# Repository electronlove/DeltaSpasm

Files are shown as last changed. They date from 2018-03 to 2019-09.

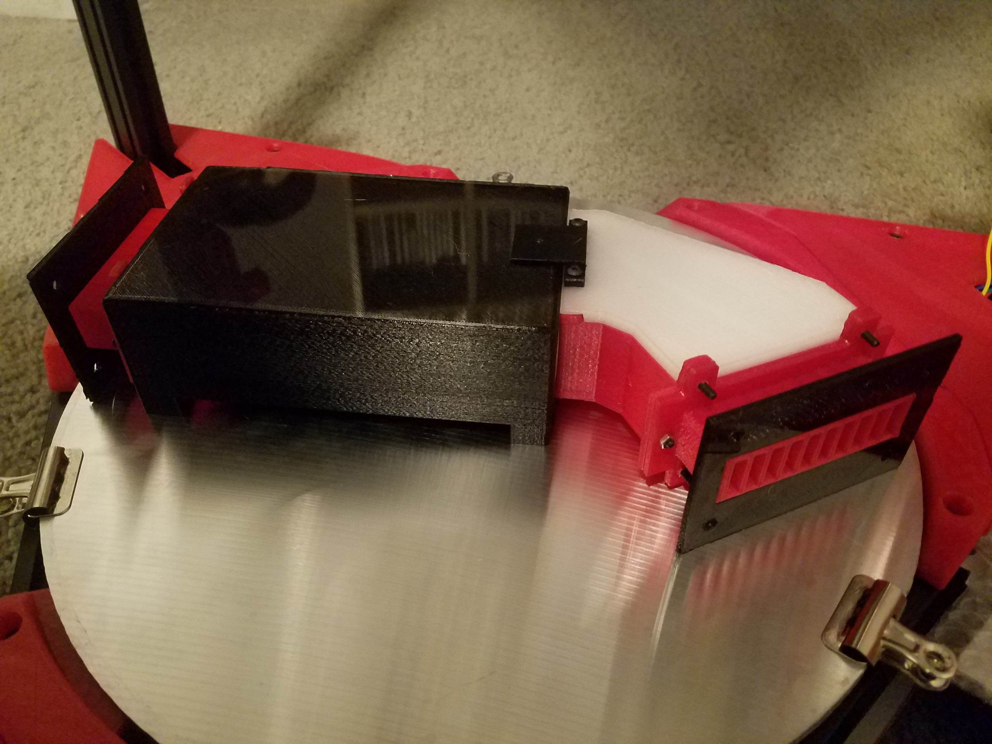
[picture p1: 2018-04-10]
Images/Cooling Fan Assembly Printed.jpg

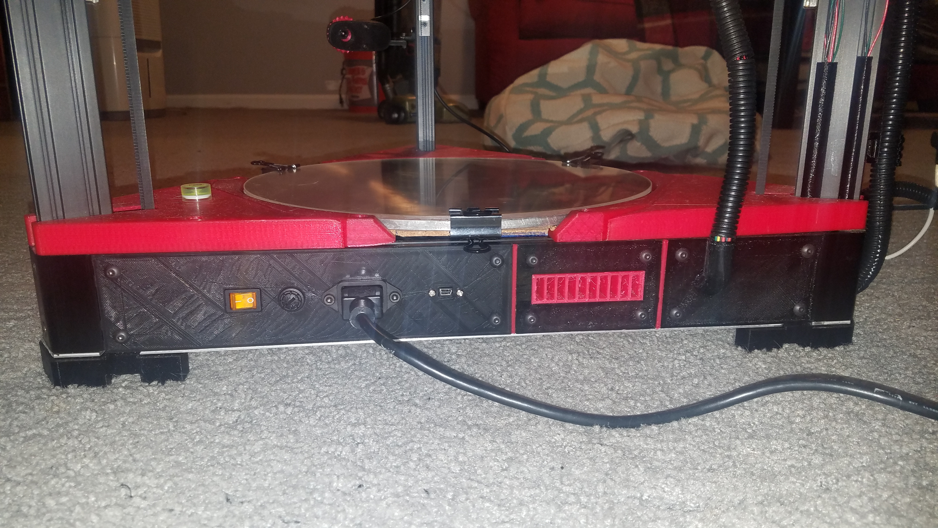
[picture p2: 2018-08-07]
Images/Delta Printer Back Panel.jpg

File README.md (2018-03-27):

# DeltaSpasm

**Larger format, 1M high Delta 3D Printer**
- **Mechanical**
  - Features a large, 310 mm build area with a 330 mm (13") x 6.25mm (0.25") MIC-6 aluminum bed.  I sourced the MIC-6 locally, from BMG Metals (Maryland).  The aluminum plate was plasma cut and the rough edges needed to be cleaned up with a Dremel !  
  - Printing surface will be 330 mm (13") x 3.175 mm (1/8") borofloat glass.  Glass will be sourced from http://www.behrenbergglass.com or www.howardglass.com at ~ $30 per plate.
  - Misumi Black Oxide 2020 and 2040 extrusions at 455mm (horizontals) and 1000mm (vertical).  
  - Delta 2040 corners from RobotDigg.  I purchased mine from an unknown Alibaba Company for a reasonable price (http://jing-bang.en.alibaba.com) 
  - 750 mm MGN12 linear rails from Jugetek (https://www.jugetek.com/) 

- **Electronics**
  - 3x 0.9° stepper motors, Model # 17HM19-1684S from Stepper Online (https://www.omc-stepperonline.com)
  - 3x Hall Endstops from Sainsmart (https://www.sainsmart.com/products/hall-effect-sensor-switch-magnetic-detector-module-for-arduino-motor)
  - 120V, 350W Silicone Heater controlled by a Crydom panel-mount SSR - Model D2425 (http://www.crydom.com/en/products/panel-mount/perfect-fit/ac-output/series-1/)
  - Meanwell 24V 350W power supply, model # LRS-350-24
  - Replicape + Beaglebone Black (https://www.thing-printer.com/)

See additional files  for BOM (xls) and STLs

Edited March 2018

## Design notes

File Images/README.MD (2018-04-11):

- The bed holders (Bed Holder.jpg) are designed to support a 13" (330 mm) x 0.25" (6.25 mm) aluminum tooling plate that is heated by a 310 mm silicone heater.  There is 13 mm clearance to accomodate (a) 6.35 mm aluminum plate (b) 4 mm cork sheet (c) 3.175 mm glass plate.  One of the bed holders is notched to allow for clearance of the bed heater wires and thermistor.  
- A set of motor covers (See *.jpg files - Motor Covers Bottom and Top for differences) prevent debris from falling into the stepper motors and finish off the top of the printing surface.  There are two types, one of which has increased clearance on the sides to accomodate wires running along the sides of the 2040 extrusions

- Hall Endstops (Hall endstop.jpg) are mounted to holders and include modified carriages that accomodate small N50 super magnets

- The Cooling Fan Assembly (Cooling fan Assembly Printed.jpg) is designed for use with Beaglebone Black and Replicapae to keep the electronics isolated from the bottom of the bed heater and motor compartments and provide for directed cooling.  It may be necessary to include an additional fan for a push/pull configuration.

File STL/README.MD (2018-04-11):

**Information on STL files**

**Endstop Holders**
- https://www.thingiverse.com/thing:2842147
- Two parts - Hall endstop holder and modified carriage with mounting point for neodymium magnets
- **File names:** Delta Hall Holder.stl and Delta_carriage_DSM.stl (Print 3X of each)

**Print Bed Surface**
  - The print bed holders are two types, one has a notch for the AC mains + thermistor wire of a silicone heater to go underneath the print bed and the other two do not.
  - 4mm thick cork should be glued in place to protect the mounts from heat damage (Mine were printed in PETG but ABS or ASA is preferable)
  - Holders use 5mm socket cap screws and t-nuts.
  - Designed to accommodate a 330 mm (13") bed and 455mm horizontal extrusions.
  - **File names:** Delta Bed Holder V1.stl (Print 2X) and Delta Bed Holder wire guide 15mm.stl (Print 1X)
  
**Motor Covers**
  - The motor covers are of two types, one has a larger notch to accomodate wiring and guide it beneath the print bed.  
  - Motor covers use 5mm socket cap screws and t-nuts.
  - Designed to accommodate a 330 mm (13") bed and 455mm horizontal extrusions.  
  - **File names:** Delta motor covers normal clean.stl (Print 2X) and Delta motor covers wire  clean.stl (Print 1X)
  
**Electronics Cooling**
  - https://www.thingiverse.com/thing:2855541
  - Consists of 2x fan grills that are 20mm in height, a fan mount for 2x 30mm fans, and a cover for BBB + replicape
  - The BBB + cape are screwed into the bottom aluminmum bottom plate / heatsink) with brass stand-offs.
  - **File names:** Fan conduit Cover V2.stl, Fan Conduit.stl, Fan Grill.stl, Cape enclosure.stl 
 
 **Other Mechanical Parts**
  - 3X Feet to raise the bottom of the Delta Printer for optional airflow in the bottom compartment and vibration isolation
  - **File names:** Delta Feet.stl
  - Panel for IEC connector, Bulgin fuse holder(Part # FX0462), and Illuminated Mains Switch (Part # H8553VBBA3-551W)
  - **File name:** Delta Power Panel.stl 
  - Panel for Panel Mount Ethernet and USB cables to Beaglebone Black (Adafruit Part # 909 and 908)
  - **File name:** ENET USB Panel.stl
  - Bottom design/heatsink for electronics and mounting holes - For CNC/laser/plasma what-have-you
  - **File name:** Delta_09_mount_t.dxf

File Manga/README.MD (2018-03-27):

**Display enclosure for 5.8" Manga Screen**

See also https://www.thingiverse.com/thing:2810512

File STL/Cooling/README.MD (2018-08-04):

Info for the Cooling Unit and Electronics Mounts

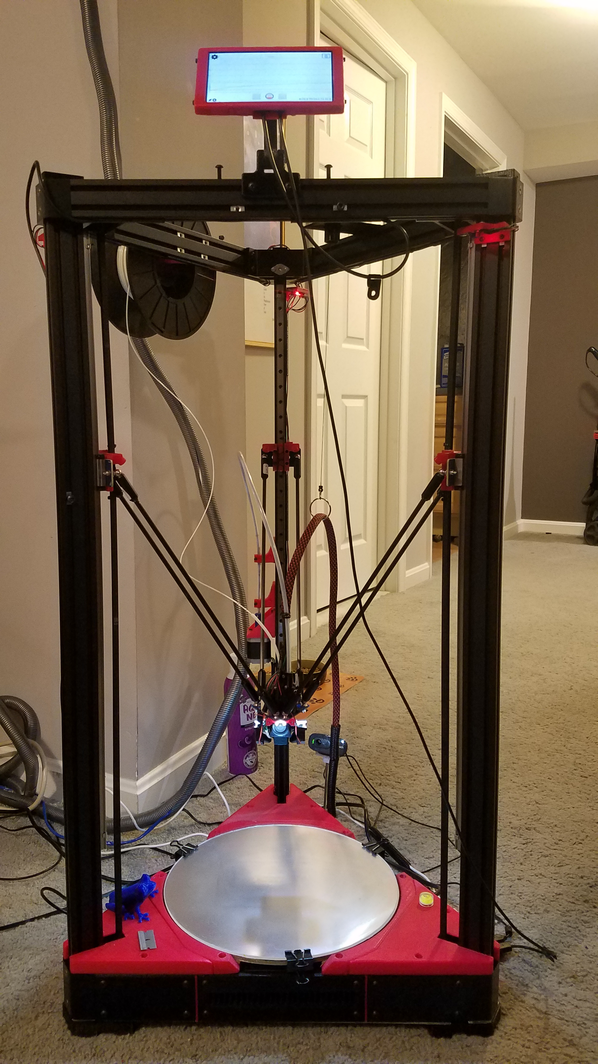
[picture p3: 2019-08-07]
DeltaSpasm_082019.jpg

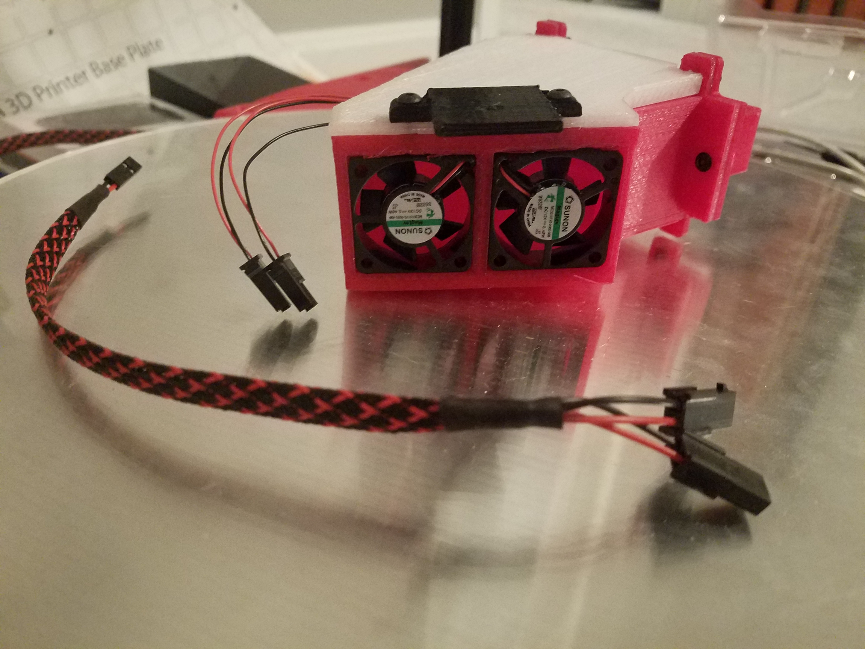
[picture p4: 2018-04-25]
Images/Cooling Fans.jpg

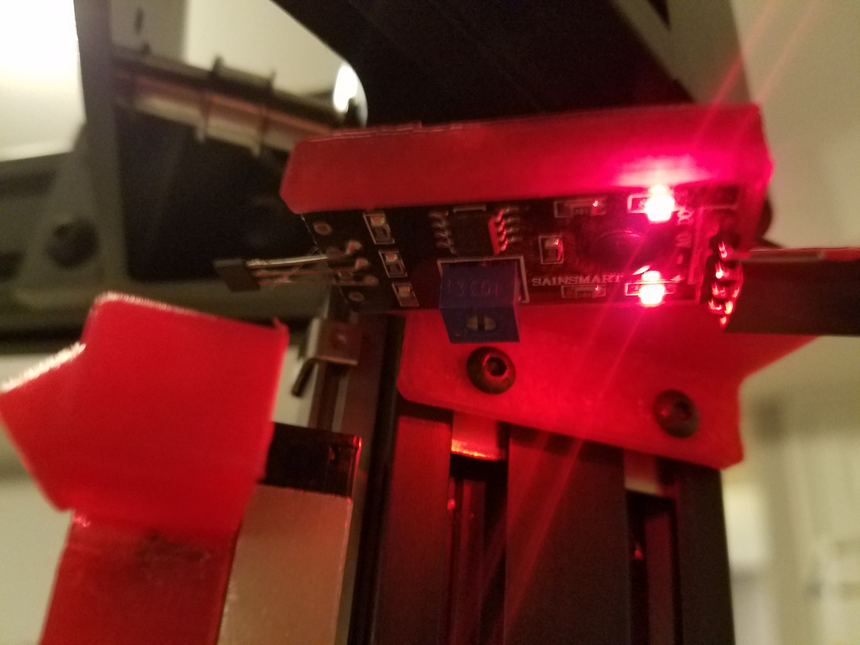
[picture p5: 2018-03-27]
Images/Hall Endstops Active.jpg

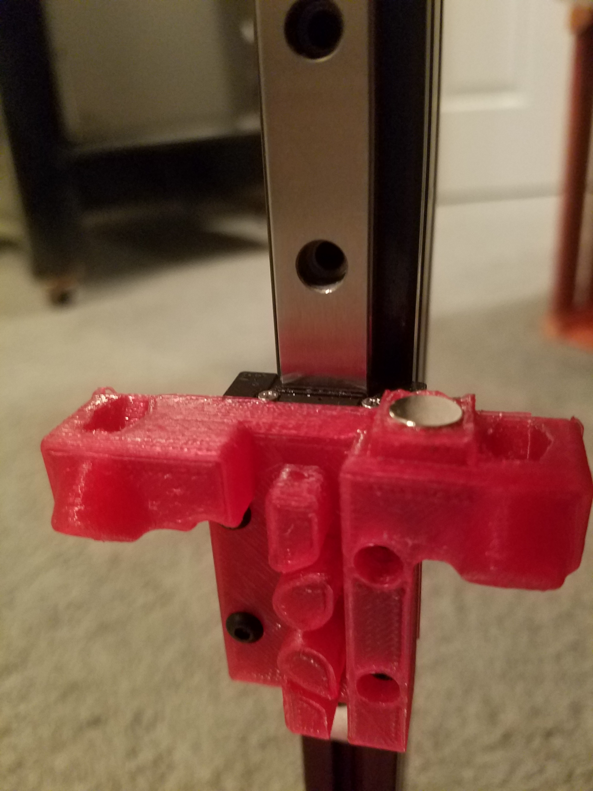
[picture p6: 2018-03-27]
Images/Carriage with N50 magnets.jpg

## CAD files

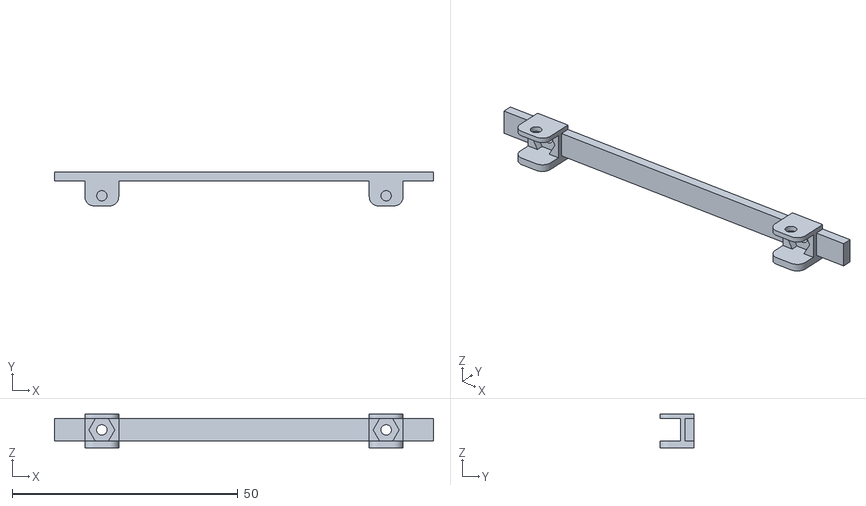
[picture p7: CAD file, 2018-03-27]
Manga/Case Brace Assembly.stl
84.0 x 7.50 x 7.50

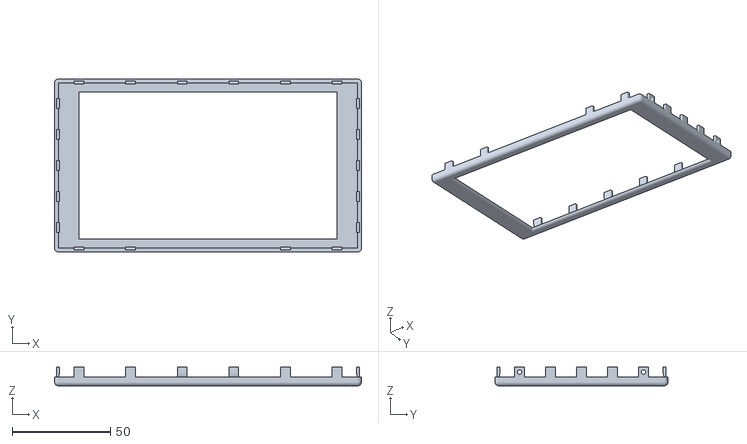
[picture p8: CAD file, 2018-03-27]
Manga/Bezel V2.stl
156.0 x 88.0 x 9.50

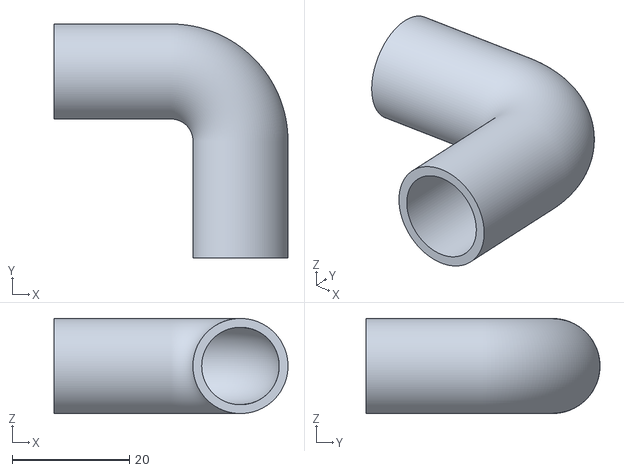
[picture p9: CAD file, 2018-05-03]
STL/Effector Wire Conduit.stl
40.0 x 40.0 x 16.2

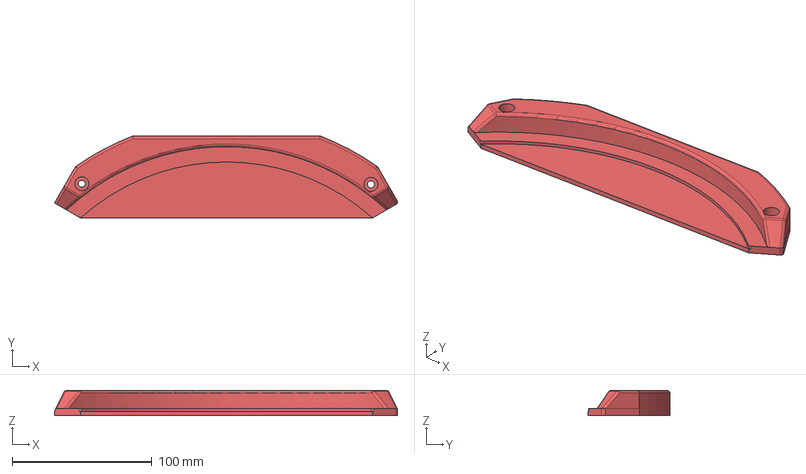
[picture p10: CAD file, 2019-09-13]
CAD/Delta Bed Holder without guide.stp
245.3 x 58.6 x 18.0 mm

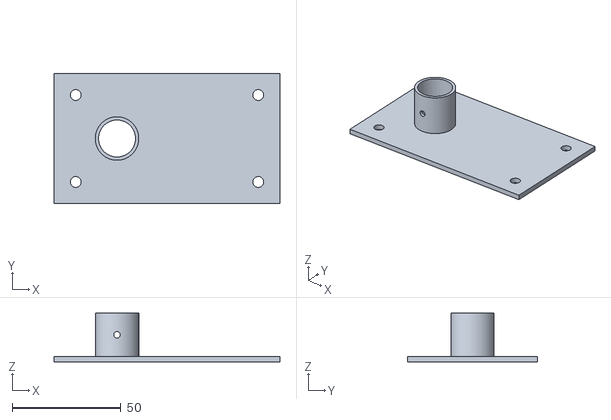
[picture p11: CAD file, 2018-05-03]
STL/Effector Wire Panel Mount.stl
104.0 x 60.0 x 22.5

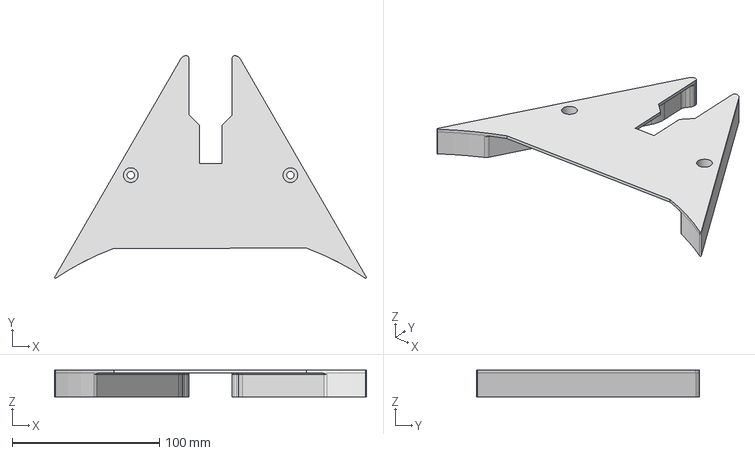
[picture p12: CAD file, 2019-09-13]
CAD/Delta motor covers wire cutout.stp
211.6 x 151.1 x 18.0 mm

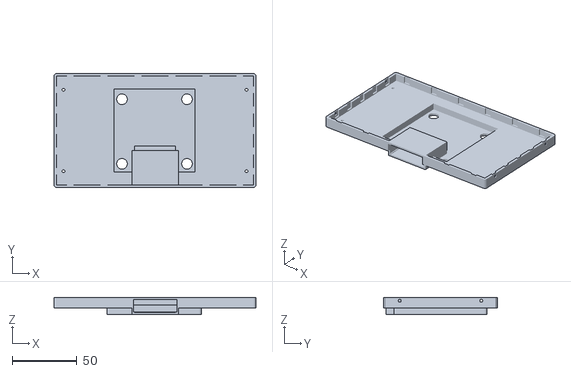
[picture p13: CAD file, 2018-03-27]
Manga/LCD bottom 10mm x 33.2mm.stl
156.0 x 88.0 x 13.2

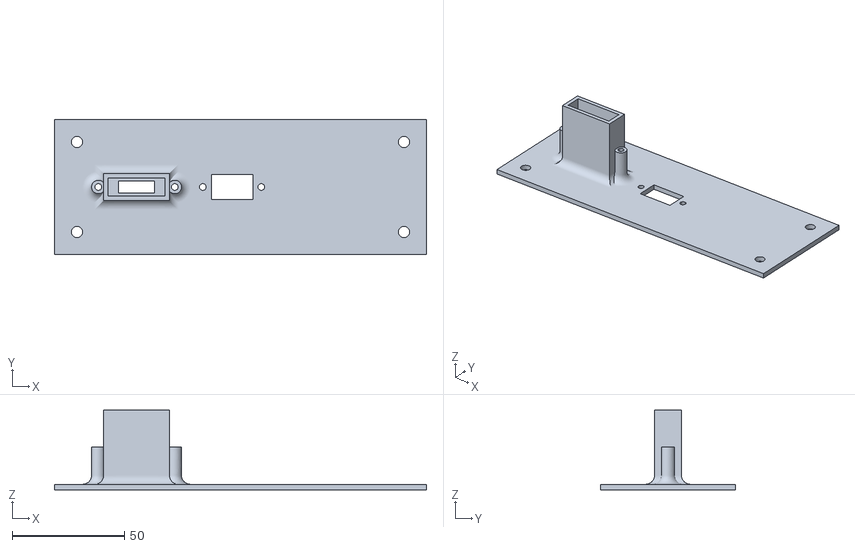
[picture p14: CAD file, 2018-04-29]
STL/HDMI mSD Panel Mount 1.stl
165.5 x 60.0 x 35.5

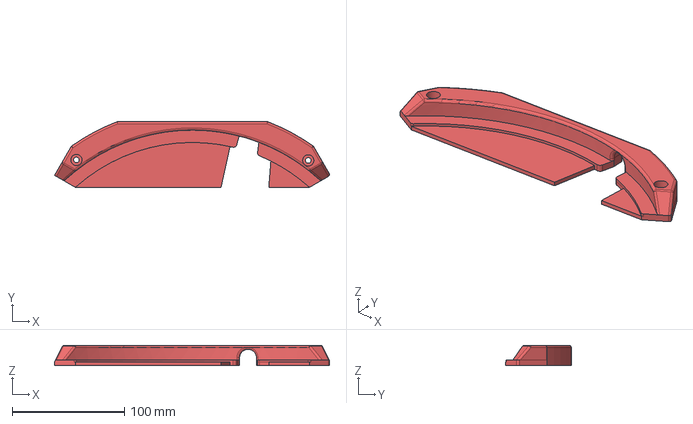
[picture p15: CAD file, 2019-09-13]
CAD/Delta Bed Holder wire guide 15mm.stp
245.3 x 58.6 x 18.0 mm

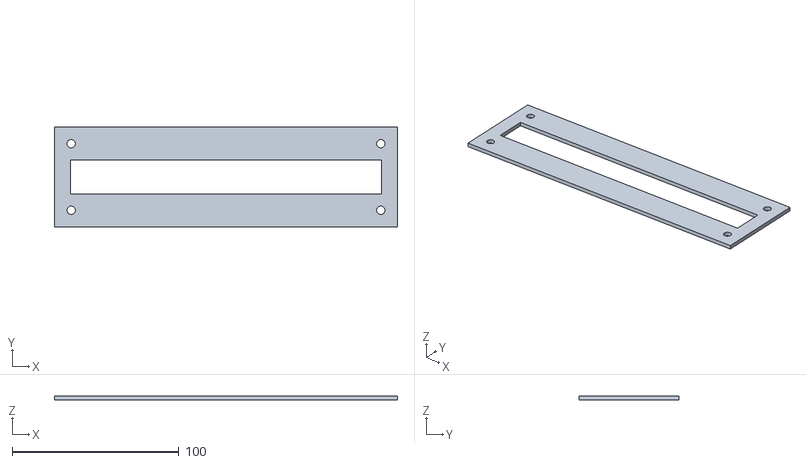
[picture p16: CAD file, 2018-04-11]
STL/Power Supply Fan Cover.stl
206.0 x 60.0 x 2.50

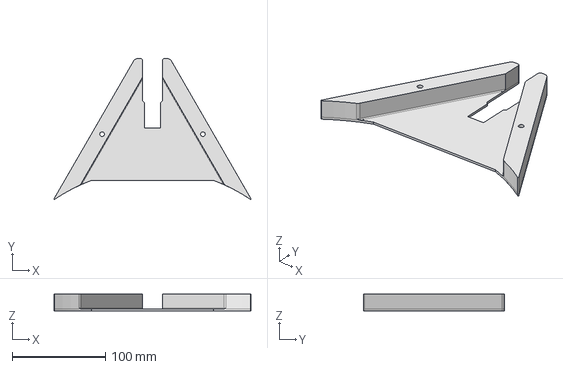
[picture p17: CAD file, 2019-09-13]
CAD/Delta motor covers.stp
211.6 x 151.2 x 18.0 mm

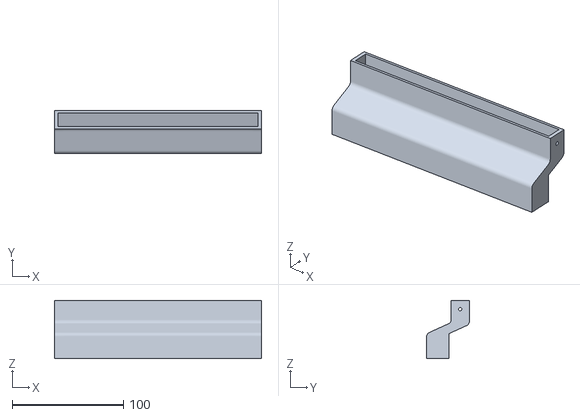
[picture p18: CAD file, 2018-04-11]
STL/Power Supply Fan V2.stl
186.0 x 38.4 x 52.5

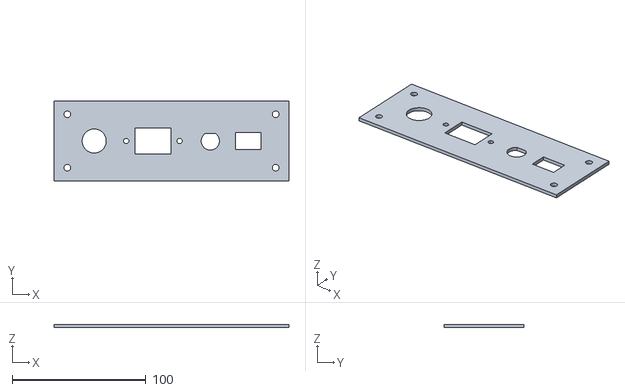
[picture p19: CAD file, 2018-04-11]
STL/Delta Power Panel.stl
176.0 x 60.0 x 2.50

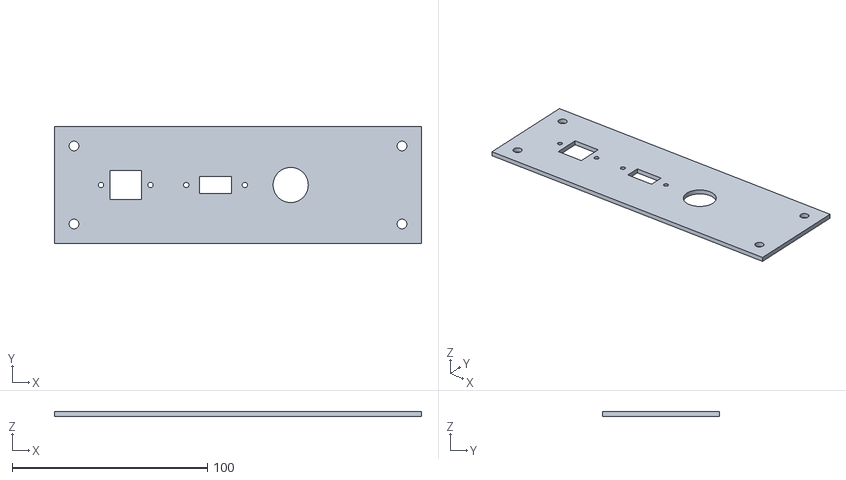
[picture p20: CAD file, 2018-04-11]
STL/ENET USB PANEL.stl
188.0 x 60.0 x 2.50

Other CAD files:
CAD/Delta bottom plate.stp
STL/Grill Cover.stl
STL/Delta Feet.stl
STL/Enclosure clip simple.stl
CAD/Delta Bed Holder wire guide 15mm.ipt
CAD/Delta Bed Holder without guide.ipt
CAD/Delta bottom plate.ipt
CAD/Delta motor covers wire cutout.ipt
CAD/Delta motor covers.ipt
STL/Cape enclosure.stl
STL/Delta Bed Holder V1.stl
STL/Delta Bed Holder wire guide 15mm.stl
STL/Delta Hall Holder.stl
STL/Delta motor covers normal clean.stl
STL/Delta motor covers wire clean.stl
STL/Delta_09_mount_t.dxf
STL/Delta_carriage_DSM.stl
STL/Fan Conduit Cover V2.stl
STL/Fan Conduit Cover.stl
STL/Fan Conduit.stl
STL/Fan Grill.stl
STL/NCdelta_SSR_cover.stl

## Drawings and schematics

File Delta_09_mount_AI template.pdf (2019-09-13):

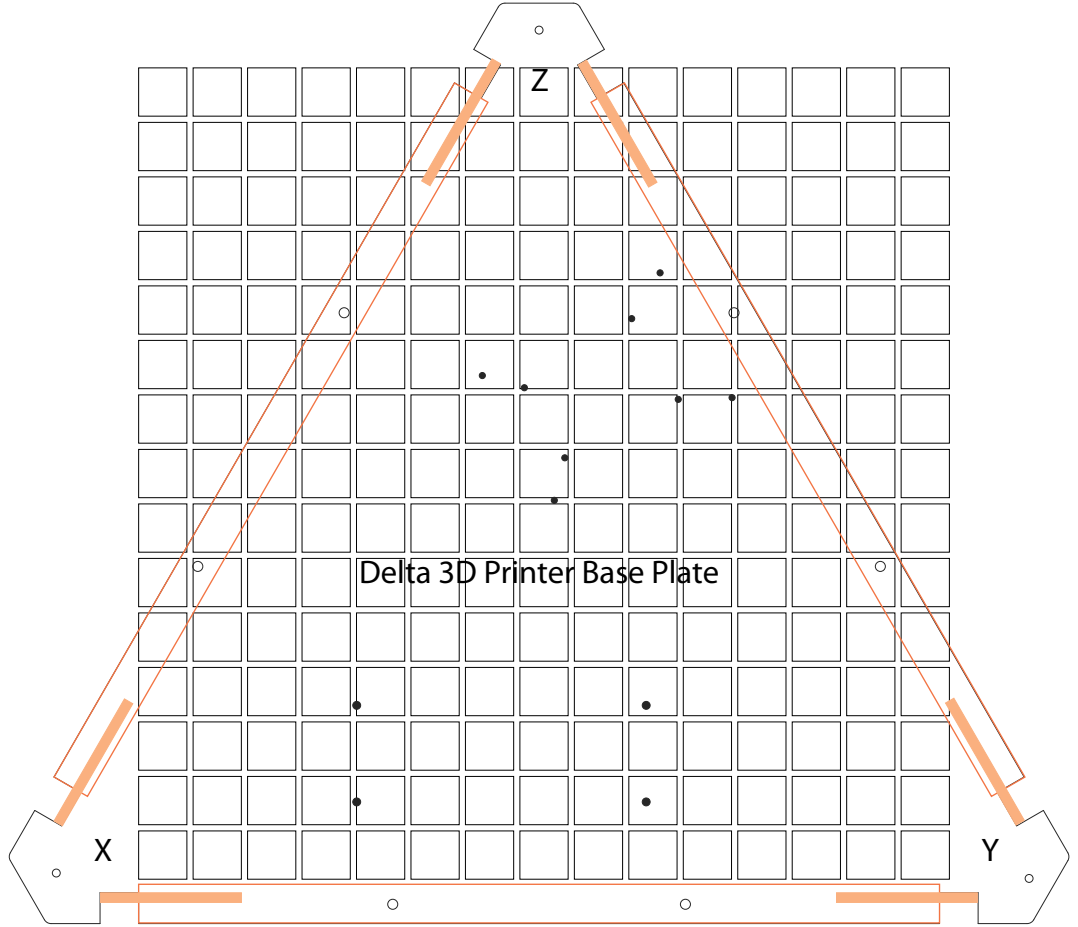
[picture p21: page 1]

Delta 3D Printer Base Plate

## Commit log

2018-03-27 Create STL
2018-03-27 Add files via upload
    Mounts for 2 x 30mm cooling fans for replicape + beaglebone black
    [Fan Conduit.stl]
2018-03-27 Add files via upload
    Requires 2x for cooling. Mounting to 2020 Alu extrusions
    [Fan Grill.stl]
2018-03-27 Add files via upload
    Mockup of Delta cooling assembly
2018-03-27 Add files via upload
    Bottom mounting plate and "heatsink"
    [Delta_09_mount_t.dxf]
2018-03-27 Add files via upload
    SSR Cover
    [NCdelta_SSR_cover.stl]
2018-03-27 Add files via upload
    Delta Printer Motor Covers
2018-03-27 Add files via upload
    Aluminum Bed Holder Mount - for 330 mm (13")
2018-03-27 Add files via upload
    Printer Build as of March 27 2018
2018-03-27 Add files via upload
    Printer build as of March 27, 2018
2018-03-28 Add files via upload
    Rendering of Delta Cooling Assembly
2019-08-07 Completed Delta Printer
2019-08-07 Current version of Delta printer
